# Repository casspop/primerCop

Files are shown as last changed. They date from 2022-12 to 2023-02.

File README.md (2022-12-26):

# PrimerCop

## A primer watchdog for a Hornady Lock-n-Load AP press

**The Problem:** If you forget to press the handle forward at the end of a loading cycle, 
the primer is not seated in the case.  

On a progressive press this is a problem.
It is a problem because the next step in the process is loading powder.  If there is not a primer plugging the primer cup when your 'finished' round is ejected into the tray, powder starts falling out the case generally making a mess.

That's why I designed PrimerCop.  It keeps track of how many primers I've used (secondary function), and it emits a long beep until I press the arm forward to seat the primer (primary function).

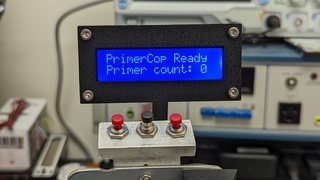
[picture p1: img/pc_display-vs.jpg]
PrimerCop display Introducing PrimerCop.

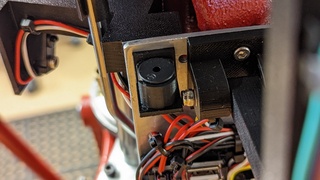
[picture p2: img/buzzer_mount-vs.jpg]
Closeup of the buzzer mount Closeup of the buzzer mount.

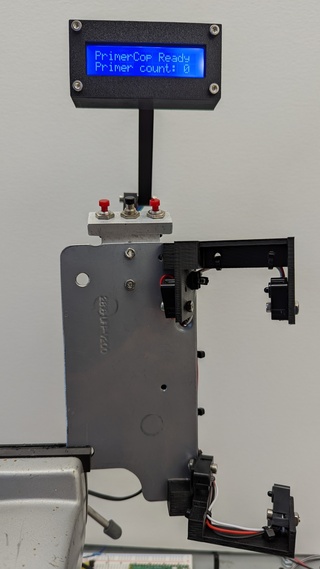
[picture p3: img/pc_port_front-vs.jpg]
portrait front Version 1.5 portrait.

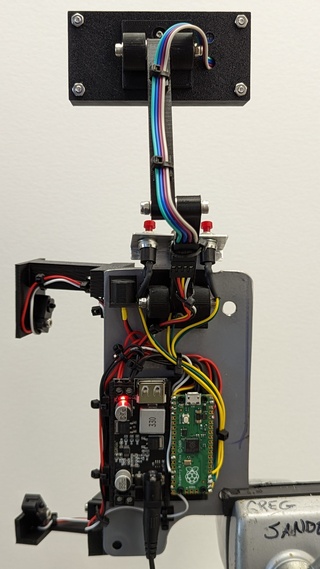
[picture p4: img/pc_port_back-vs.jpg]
portrait back Version 1.5 portrait.


All images are [here on the /img readme.md](./img/readme.md).

PrimerCop uses two sets of Adafruit IR break-beam sensors which are triggered at the top and bottom of the cycle.

A Drok buck converter provides power to a Raspberry Pi Pico microcontroller running a Micropython app I wrote.

The mounts for everything are designed in OpenSCAD and are currently printed in PLA on a Prusa Mk3s.  I had thought I might want to print the parts with ABS, but after trying it once, I decided to stick with PLA because it is stiffer, not to mention easier.

The whole thing is built on a steel plate that bolts to the press with two 1/4-20 bolts screwed into the factory provided holes on the back of the press.

This makes for easy removal of the entire unit for any reason at any time.

### Changelog
**12/23/22** - v1.1.0 of bottom bracket.  The primer slide wheel was contacting it ever so slightly, but it was enough to cause a problem. This mod takes care of that.</br>
             - v2.1.0 of main.py removes some unnecessary lines that were slowing things down.  Adding and subtracting to the count is quicker now.

**12/8/22** - Version 2 of the Pi Pico software is working and available in the Code
section.  Three hardware buttons were added. Two of them allow for adding or subtracting from the 'primercount' variable.  The third button resets everything.

Debouncing the buttons is done in software, and works pretty good.

**12/6/22** - Version 1 of PrimerCop is functioning.  It's not what I'd call ready
for prime time, but it does work.

I'm working on getting a set of 3 buttons added.  Designing the mounting
solution for the buttons is the task du jour.

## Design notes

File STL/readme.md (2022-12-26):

# STL Files

Here are the STL files I used on the Prusa Mk3s with PLA.

Be aware that the tolerances on these are tight.  You can construct the device using these STL's, but the hardware will go in only with some insistence on your part.  See the [readme.md in the docs folder](https://github.com/casspop/PrimerCop/blob/master/docs/Function%20and%20Assembly%20Notes.md) for more details.

Base for articulating arm (2 are needed). [ArticArm1602_base.stl](./ArticArm1602_base.stl)

Articulating arm section (2 needed). [ArticArm1602_sect.stl](./ArticArm1602_sect.stl)

Plastic version of my metal base plate. [horn_primercop_plate.stl](./horn_primercop_plate.stl)

Bottom of LCD mount. [hornady_1602_LCD_mount_bottom.stl](./hornady_1602_LCD_mount_bottom.stl)

Top of LCD mount. [hornady_1602_LCD_mount_top.stl](./hornady_1602_LCD_mount_top.stl)

Holder for electronics. [hornady_ap_primerCop_electronics-mnt.stl](./hornady_ap_primerCop_electronics-mnt.stl)

Top IR break-beam mount. [hornady_ap_primerCop_Top.stl](./hornady_ap_primerCop_Top.stl)

Bottom IR break-beam mount. [hornady_ap_primerCop.stl](./hornady_ap_primerCop.stl)

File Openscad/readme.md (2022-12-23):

# OpenSCAD files.

Built with [OpenSCAD](https://www.openscad.org).

These are the files I used to print the parts for PrimerCop.  

They are a bit tight on the hardware, but I was able to put it together.

I'm planning on adding about 1mm to the Drok power supply mount space as well
as the enclosure and faceplate for the LCD display.  I'll update these when
I do that, but it may be January or February 2023 before I get around to it.

- **1602A-4 LCD.scad** - the 16-character 2-line LCD module w/ i2c module attached.</br>
- **3mmSocketHeadHole.scad** - dependancy of several of these files.</br>
- **ArticArm1602_base.scad** - articulating arm base.</br>
- **ArticArm1602_sect.scad** - articulating arm section.</br>
- **horn_primercop_plate.scad** - renders the steel mounting plate. Corrected 12/10/22.</br>
- **hornady_1602_LCD_mount.scad** - The housing and faceplate for the 1602 LCD.</br>
- **hornady_ap_primerCop_electronics-mnt.scad** - mount for Drok and Pico.</br>
- **hornady_ap_primerCop_Top.scad** - top bracket for IR break-beams.</br>
- **hornady_ap_primerCop.scad** - bottom bracket for IR break-beams. v1.1.0 mod to avoid slide wheel.</br>
- **hw-061 i2c LCD module.scad** - i2c module. Goes with the LCD module.</br>
- **piezobuzzermount.scad** - mount for standard piezo buzzer.</br>
- **tinyZipTieMnt.scad** - glue these where you want to use a tiny zip tie.</br>

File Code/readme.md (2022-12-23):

# readme.md - What is What

**PrimerCop_Final_v2.1.1.py** - the Micropython software.  
v2.1.1 removed some unnecessary actions that slowed things down.
Rename this file to 'main.py' and upload it to the Pi Pico.

**lcd_api.py** - one of two driver files required.  Copy to the Pico.

**pico_i2c_lcd.py** - the second required file.  Copy to the Pico.

The two dependancy files are from here: [dhylands Github](https://github.com/dhylands/python_lcd)

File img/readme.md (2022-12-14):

# Images

Display
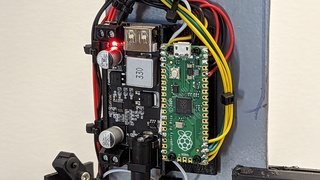
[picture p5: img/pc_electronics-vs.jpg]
Electronics

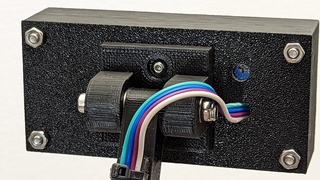
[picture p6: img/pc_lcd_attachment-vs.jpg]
LCD Attachment

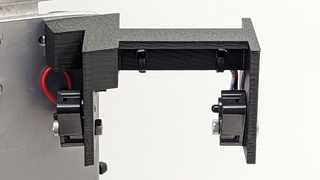
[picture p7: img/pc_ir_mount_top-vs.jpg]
Top Ir Mount

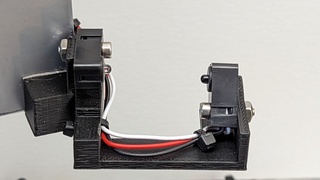
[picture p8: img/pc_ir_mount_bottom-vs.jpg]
Bottom Ir Mount

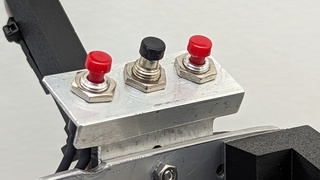
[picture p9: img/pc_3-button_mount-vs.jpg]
3-button mount.

Buzzer mount.
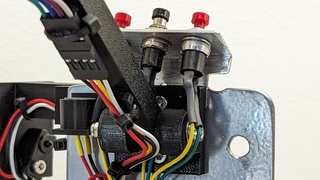
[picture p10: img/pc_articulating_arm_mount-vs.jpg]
Articulating arm mount.
</br>
Front View
Back View
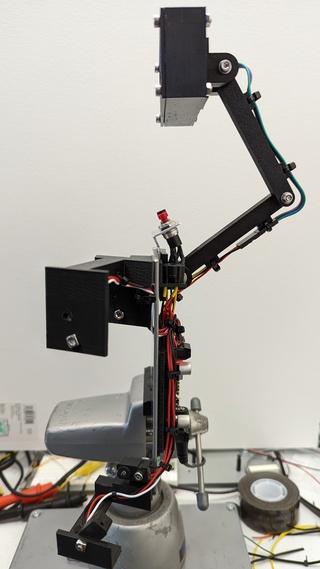
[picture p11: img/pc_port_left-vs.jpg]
Left Side View

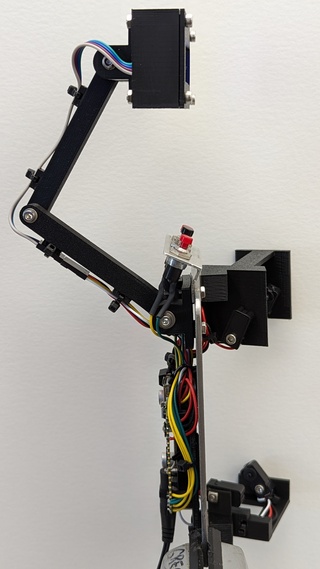
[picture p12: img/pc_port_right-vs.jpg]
Right Side View

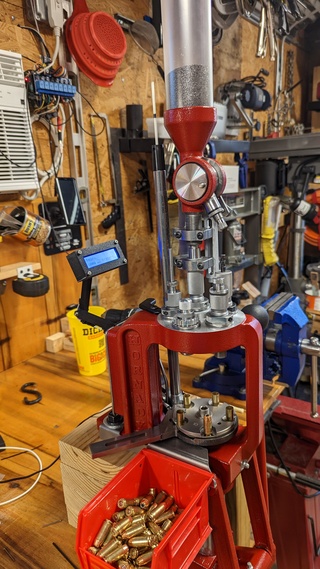
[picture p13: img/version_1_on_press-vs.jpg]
Version 1 hardware mounted on press.


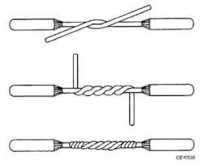
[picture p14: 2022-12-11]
img/lineman-splice.jpg

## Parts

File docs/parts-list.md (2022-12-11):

# Parts List

These are the parts I used to put this together.  Some of them, like fasteners and standoffs, are from kits I have on hand which were purchased for other projects.

The 3mm (1/8") plate I used as the primary mounting plate is a recycled VESA mount adapter plate from a flat panel display mounting kit I acquired years (decades!) ago.  As usual, I use what I have when I can.

All links below are for your convenience.  I get nothing from anyone for posting them. (CTRL-click links to open in new window.)

## The Parts

- [Raspberry Pi Pico](https://www.sparkfun.com/products/17829?src=raspberrypi) - $4.00 - the 'W' is not needed for this project.
- [Drok Buck Converter](https://www.amazon.com/gp/product/B01NALDSJ0/ref=ppx_yo_dt_b_search_asin_title?ie=UTF8&psc=1) - $9.99 - 12vdc to 5vdc power supply.  Plug a 12vdc wall wart in and you're ready to go.  You do have a bunch of those in a box somewhere, right?  I use this power supply a lot in my Pi projects.
- [Adafruit IR break-beam sensors](https://www.adafruit.com/product/2167) - $2.95 per set - Buy at least two sets, one for the top and one for the bottom.  I recommend having a spare in case you mess up.
- [SPST Momentary pushbuttons](https://www.amazon.com/dp/B0BHCLHNKR?psc=1&ref=ppx_yo2ov_dt_b_product_details) - $9.99 for 12 - Need three, but they're good to have on hand.  I like these with the pigtail already soldered on.  Convenient.
- [1602 LCD with i2c module](https://www.amazon.com/KEYESTUDIO-Display-Arduino-Raspberry-Stm32/dp/B0177XQE7K) - $9.99 - This is not the exact one I used, but they are very standardized, so it should be fine.
- [M3 Hex Socket Head screws](https://www.amazon.com/gp/product/B07J44YXV3/ref=ppx_yo_dt_b_search_asin_title?ie=UTF8&psc=1) - $21.99 for 700 piece kit - You really need to have these on hand.
- [M2.5 Stainless Steel Button Head Socket Cap Screws](https://www.amazon.com/gp/product/B076ZN18KZ/ref=ppx_yo_dt_b_search_asin_title?ie=UTF8&psc=1) - $11.99 for 240 pieces - Great kit.
- [M2.5 Nylon Standoffs](https://www.amazon.com/gp/product/B07D78PFQL/ref=ppx_yo_dt_b_search_asin_title?ie=UTF8&psc=1) - $14.88 for 320 piece kit - Again, invaluable if you're doing much project work like this.
- [4" Zip Ties](https://www.amazon.com/s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) - $5-7 - Nothing special here.  Home Depot, Lowes, Ace Hardware.
- [Gorilla Mounting Tape](https://www.amazon.com/Gorilla-Heavy-Double-Sided-Mounting/dp/B082TQ3KB5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) - $12.24 for 120 inches - This stuff is fantastic if you want a thing to stay where you put it.  Available nearly anywhere.
- [Stainless washers](https://www.amazon.com/gp/product/B009OK7GPO/ref=ppx_yo_dt_b_search_asin_title?ie=UTF8&psc=1) - $6.16 for 100 - Needed for articulating arm joints.  You can use other things, but these are what I have.
- [M3 Stainless NyLock Nuts](https://www.amazon.com/100Pcs-Stainless-Self-Lock-Inserted-Clinching/dp/B075ZZW7VL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) - $6.99 for 100 - Use on articulating arm pivot points.
- [3/4" Aluminum angle stock 1/8" thick](https://www.homedepot.com/p/Everbilt-3-4-in-x-36-in-Aluminum-Angle-with-1-8-in-Thick-801397/204273997) - $11.47 for 36" - Need about 2" of this, but again, it's good to have on hand.  Used for the switch mount.
- Heat Shrink Tubing of appropriate sizes.  Get an assortment set if you don't have some already.

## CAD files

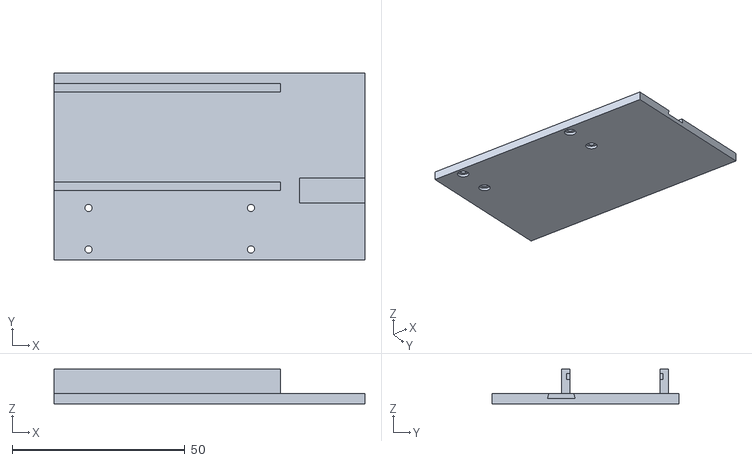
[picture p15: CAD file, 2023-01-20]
STL/hornady_ap_primerCop_electronics-mnt.stl
90.0 x 54.0 x 10.0

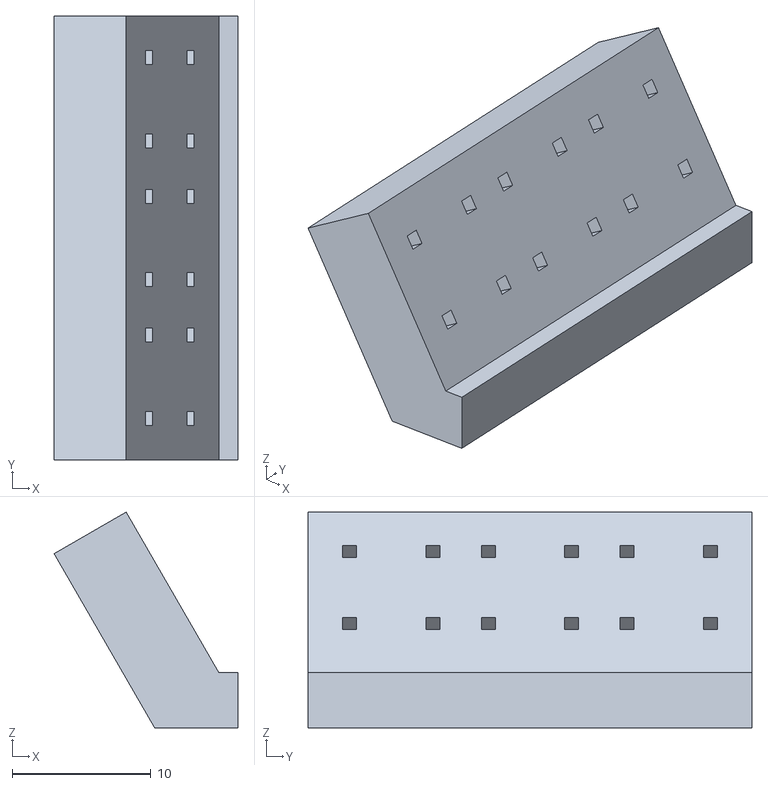
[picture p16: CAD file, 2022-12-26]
STL/horn_PrimerCop_buttons_base.stl
13.2 x 32.0 x 15.6

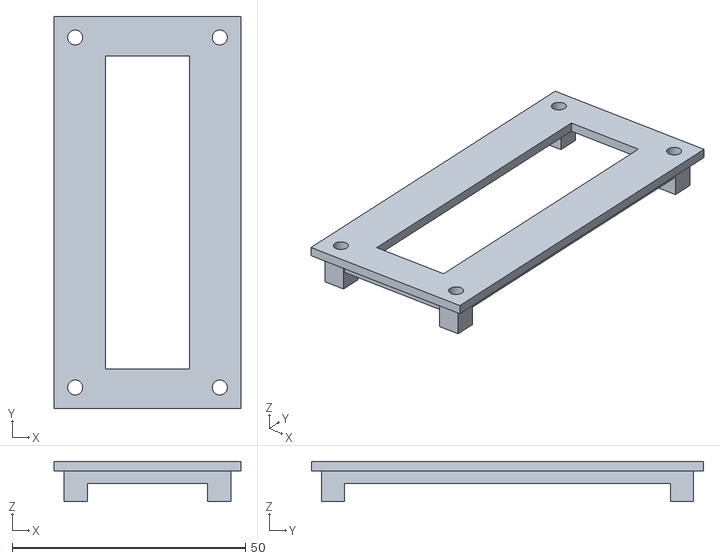
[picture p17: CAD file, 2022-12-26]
STL/hornady_1602_LCD_mount_top.stl
40.0 x 84.0 x 8.60

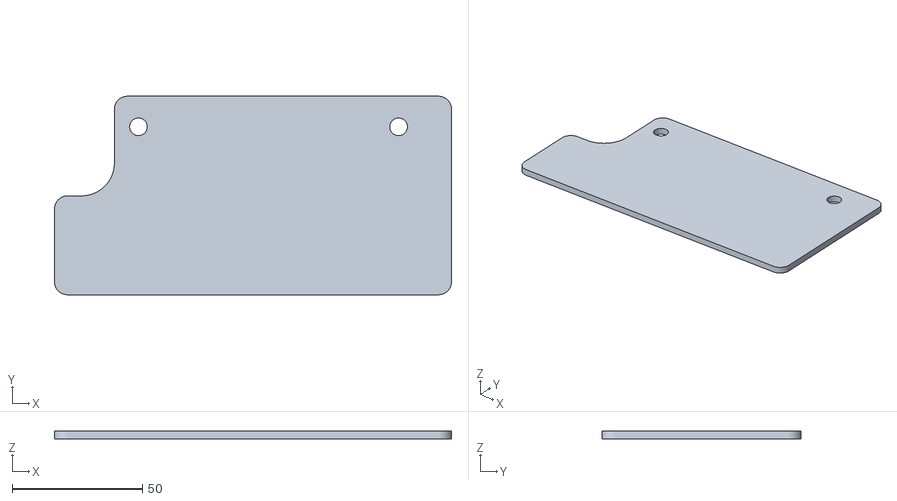
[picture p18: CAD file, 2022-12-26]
STL/horn_primercop_plate.stl
152.5 x 76.3 x 3.00

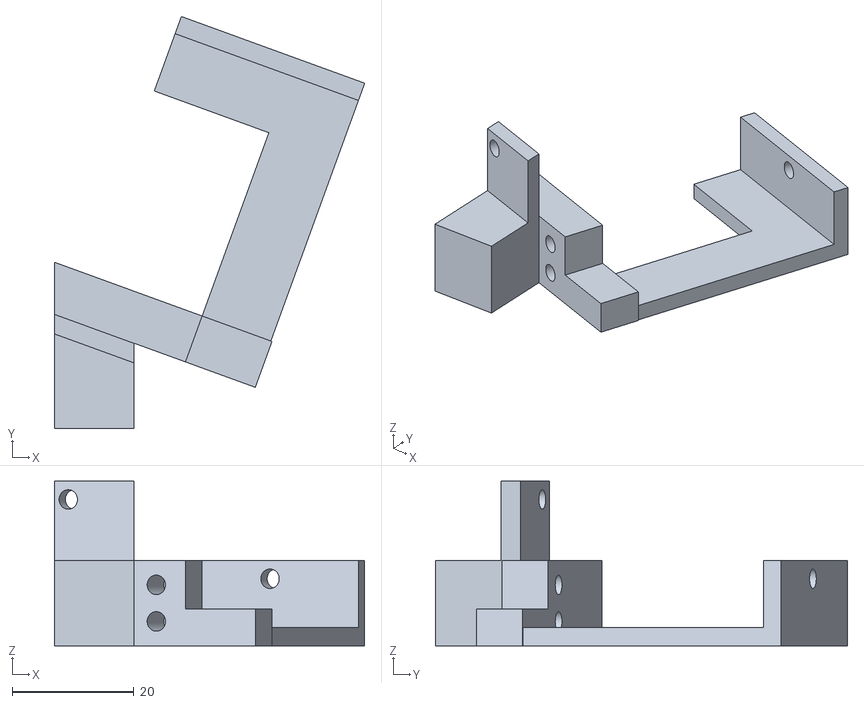
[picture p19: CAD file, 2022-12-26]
STL/hornady_ap_primerCop.stl
50.9 x 67.6 x 27.0

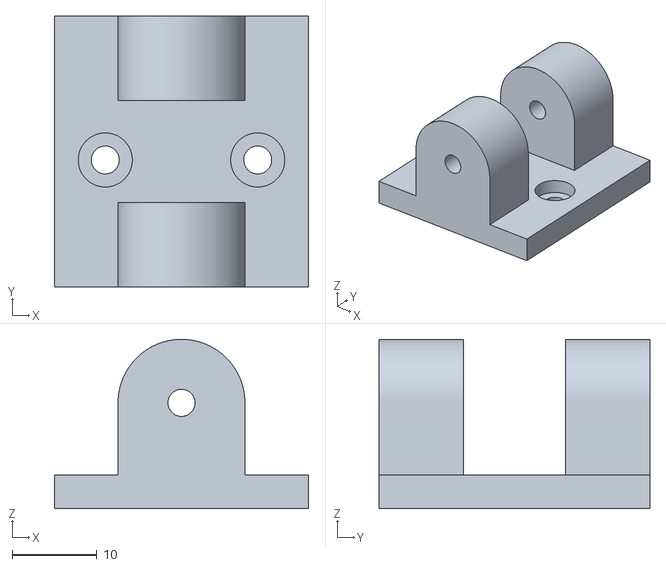
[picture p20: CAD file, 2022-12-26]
STL/ArticArm1602_base.stl
30.0 x 32.0 x 20.0

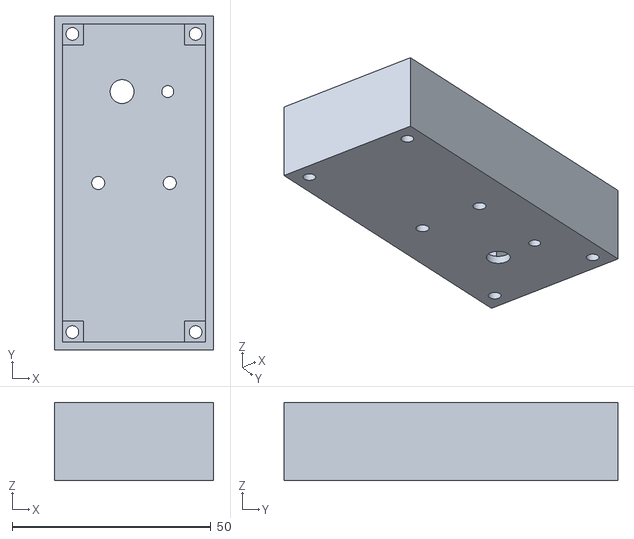
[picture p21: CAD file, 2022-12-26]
STL/hornady_1602_LCD_mount_bottom.stl
40.0 x 84.0 x 19.7

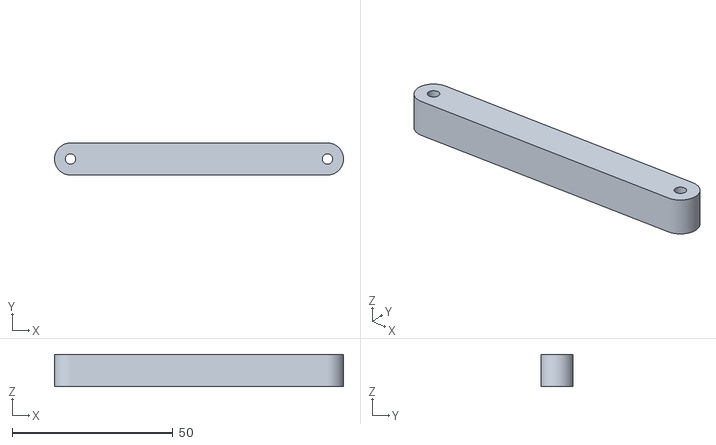
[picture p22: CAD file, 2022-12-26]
STL/ArticArm1602_sect.stl
90.0 x 10.0 x 10.0

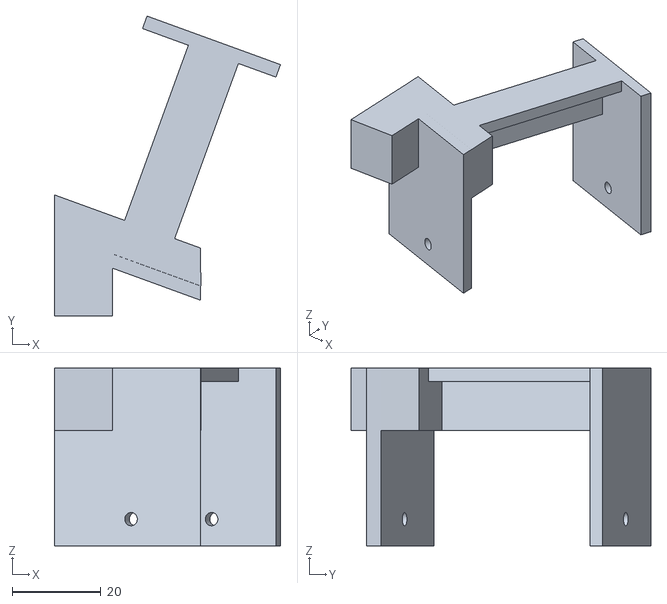
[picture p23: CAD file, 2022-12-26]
STL/hornady_ap_primerCop_Top.stl
50.9 x 67.6 x 40.0

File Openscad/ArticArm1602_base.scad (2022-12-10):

// ArticArm1602_base.scad - Articulating Arm Mount for 1602A LCD
// 2022 Gregory A Sanders
//
//
// hole for 3mm machine screw = 3.2
//

use <3mmSocketHeadHole.scad>

$fn=120;
module base(){
    difference(){
        cube([30,32,4]);
        rotate([180,0,0])
        translate([6,-15,-6])
        SocHdHole();      
        rotate([180,0,0])
        translate([24,-15,-6])
        SocHdHole();

    }
}

module pivot(){
    difference(){
        translate([0,0,12.5])
        rotate([90,0,0])
        hull(){
            cylinder(10,d=15,center=true);
            translate([0,-7.5,0])
            cube([15,10,10],true);
        }
        union(){
        translate([0,0,12.5])
        rotate([90,0,0])
        cylinder(30,d=3.2,center=true);

        }
    }
}

module aacomposite(){
    base();
    translate([15,5,0])
    pivot();
    translate([15,27,0])
    pivot();
}

aacomposite();

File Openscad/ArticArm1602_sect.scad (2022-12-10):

//ArticArm1602_sect.scad - Articulating Arm section for 1602 LCD
//2022 Gregory A Sanders
//
//
$fn=120;
module arm(){
    difference(){
    hull(){
        translate([0,5,0,])
        cylinder(10,d=10);
        cube([80,10,10]);
        translate([80,5,0])
        cylinder(10,d=10);
    }
    translate([0,5,-5])
    cylinder(20,d=3.2);
    translate([80,5,-5])
    cylinder(20,d=3.2);
}
}
arm();

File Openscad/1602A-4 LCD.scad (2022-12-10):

//1602A-4 LCD.scad - Dr.Gerg's 1602A-4 16x2 LCD module
//
// OpenSCAD definition file
// https://www.drgerg.com

use <hw-061 i2c LCD module.scad>;
holespcx = 33.86;
holespcy = 77.9;
mntholedia = 2.7;
pcb1 = [36,80,1.13];
lcd = [24.40,69.28,6.57];
lscrn = [16.28,65.19,1]; // lcd screen
lsc = [1,0.1,0];                    // lcd screen corner
LEDpoly = [[2.625,0],[15.125,0],[17.75,3.25],[17.75,5.35],[0,5.35],[0,3.25]];
module pin(tx,ty,tz,ry,cl,cx,cy){
    translate([tx,ty,tz])
    rotate([0,ry,0])
    cube([cl,cx,cy],false);
    translate([-2,-1,5])
    color("black")
    cube([40.5,2.54,2.54],false);
}
module screen(){
    minkowski(){
        cube([lscrn.x - lsc.x*2,lscrn.y - lsc.x*2,lscrn.z]);
        cylinder(r=lsc[0],h=lsc[1]);
    }
}
module light(){
    linear_extrude(3)
    polygon(LEDpoly);
    }
$fn=48;

module LCD1602A(){
    difference(){
    color("green")
    cube(pcb1);
    translate([(pcb1.x/2)-((holespcx-mntholedia)/2),(pcb1.y/2)-((holespcy-mntholedia)/2),0])
    cylinder(h=6,d=mntholedia,center=true);
    translate([(pcb1.x/2)+((holespcx-mntholedia)/2),(pcb1.y/2)-((holespcy-mntholedia)/2),0])
    cylinder(h=6,d=mntholedia,center=true);
    translate([(pcb1.x/2)-((holespcx-mntholedia)/2),(pcb1.y/2)+((holespcy-mntholedia)/2),0])
    cylinder(h=6,d=mntholedia,center=true);
    translate([(pcb1.x/2)+((holespcx-mntholedia)/2),(pcb1.y/2)+((holespcy-mntholedia)/2),0])
    cylinder(h=6,d=mntholedia,center=true);
    };
    translate([pcb1.x/2 - 17.25/2,0,pcb1.z])
    color("white")
    light();
    difference(){
        color("black")
        translate([pcb1.x/2 - lcd.x/2,pcb1.y/2 - lcd.y/2,pcb1.z])
        cube(lcd);
        color("blue")
        translate([pcb1.x/2 - lscrn.x/2 +lsc.x,pcb1.y/2 - lscrn.y/2 + lsc.x,lcd.z-lscrn.z+1.1])
        screen();
    }
    translate([33.3,33.9875,-7.7])
    rotate([0,0,90])
    for (i=[0:15])
        pin(i*2.54,0,0,270,12,.64,.64);
    translate([34.3,32.4,-3])
    rotate([0,180,0])
    hw061();
}

LCD1602A();

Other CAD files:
Openscad/3mmSocketHeadHole.scad
Openscad/horn_primercop_plate.scad
Openscad/hornady_1602_LCD_mount.scad
Openscad/hornady_ap_primerCop.scad
Openscad/hornady_ap_primerCop_Top.scad
Openscad/hornady_ap_primerCop_electronics-mnt.scad
Openscad/hw-061 i2c LCD module.scad
Openscad/piezobuzzermount.scad
Openscad/tinyZipTieMnt.scad

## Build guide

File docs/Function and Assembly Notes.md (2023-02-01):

# Function and Assembly Notes

**--== These notes are in progress ==--**

## Function Notes

PrimerCop is a pretty simple piece of gear.  The bar on the press that retrieves and delivers the primers moves up and down with the turret plate.  We are putting IR break-beam sensors at the top and bottom of its travel to detect its location in the cycle.

The sensor at the top is triggered by the bar blocking the IR light.  When that happens, the program provides feedback to the user and increments the counter.

As the bar moves back down, the sensor is once again exposed to the IR emitter's output, and the software provides notification of that event.

When the bar reaches the bottom of its travel, the bottom sensor is deprived of IR and the software interprets that event as a primer is ready to be seated.  The buzzer begins sounding and continues until the handle of the press is moved forward to seat the primer in the case.

Moving the handle forward lowers the turret and the bar.  This exposes the sensor to the IR source and the software stops the buzzer and informs the user that the primer has been seated.

Releasing the handle once again blocks the sensor, and the software then reports the end of the cycle and how many primers have been used to that point.

## Assembly Notes: refer to the pictures in the ./img folder for reference

### Mounting sensor brackets

The top and bottom sensor brackets are held to the mount plate with Gorilla double-sided mounting tape.  This solution seems to be more than adequate.  Of course, screws and nuts could be used, but I don't see why that would be necessary at this point.

### IR sensor notes

The sensors themselves are not mounted exactly the same on top and bottom.  That is because the little primer sled moves out into the area where the top emitter would be if it were mounted exactly like the bottom emitter.  What I did was to dry-fit the emitter with the assembled PrimerCop mounted to the press.  I determined where a hole needed to be drilled in the top bracket so the emitter's LED could cast its beam toward the receiver.  Then I drilled said hole and mounted the emitter.

### Base plate thoughts

I made my baseplate out of a steel VESA adapter plate from a TV mount.  I've had a few of these for years, and it was perfect for this application.  I cut out what I needed.

After getting the PrimerCop working, I then made the OpenSCAD model to match the dimensions of my steel plate.  I printed it out and verified its fit on the press.  I'm of the opinion at this point that a 3D printed version of that plate in PLA or PETG with no infill (solid plastic) would be adequately stiff to be used in place of the steel plate I have.  Just a thought.

### Mounting electronics

The Drok power supply and the Pi Pico are mounted to the same plate.  The Drok converter has no holes for mount screws, so I have a channel for it to slide into.  It is a bit too tight, but I was able to work it into position.  I made a version 2 of the hardware with about 1.0mm added to make it less tight. That's what is in the SCAD and STL folders now.

There are holes in the mount plate for 2.5mm standoff screws.  Attach standoffs using those screws and mount the Pico to the standoffs.

Once you have both pieces of hardware mounted to their mount plate, affix it to the steel plate with 3 or 4 smallish pieces of Gorilla mounting tape.

### Display notes

The same snugness problem that I encountered with the Drok converter reared its ugly head with the display mount.  I will be adding some space to the interior of that model as well.  It =does= fit, but it's really tight.  Not so tight as to cause alarm, but too tight for easy assembly.

I also will be enlarging and moving the LCD contrast adjustment hole to more correctly align it with the potentiometer on the i2c board.  For the time being, I simply drilled it out larger so I could access the pot.

### Wire routing

As you assemble your parts, you will need to account for routing and dressing your wires.  I created the 'tinyZipTieMnt' model and I used it in several places where I needed them to keep wires under control.

I used a typical superglue (Cyanoacrylate) product.  I noticed it seemed to take an unusual amount of time for this glue to set on the plastic.  If I could be patient or distract myself with something long enough, it would eventually set.  Once it did, it was quite permanent.

You may need to drill some holes for zip ties in some areas.  Use your own judgement.

### Wiring diagram notes

There currently is no wiring diagram.  I may fix that later, but it's not a high priority.

- The i2c circuit is typical.
- I landed 12vdc from the Drok on the VSYS pad.  I had it on the VBUS pad originally, but moved it while trying to comprehend the parameters of using USB for programming without unplugging the Drok supply.  In the end, I just left my 12vdc supply connected to VSYS.  VBUS may be a better choice, but it also has a voltage drop from a diode.  No biggie, but it is there.
- Where to land the sensors and switches can be determined by reading the Python program file.  easy peasey
- Be very careful to provide solid power and ground connections between the Drok converter and the Pico.
  - If you, like I, use the phoenix connector on the Drok, make sure you get all your conductors solidly screwed down.  
  - This does NOT mean tighten the screw more.  It means strip off enough insulation to expose enough conductor so when you twist them all together they are long enough to fit deep into the connector, but not so long as to have bare conductor sticking out more than 1/32" or so.  If you need to, pull them back out and trim them off a bit.
- I create a splice point inline when I have a bunch of wires all going to the same place.  Just twist them together using a modified [linemans splice](../img/lineman-splice.jpg) (simplified) with one wire exiting to solder to the termination point.  The appropriate piece of heat shrink tube tops it off nicely.

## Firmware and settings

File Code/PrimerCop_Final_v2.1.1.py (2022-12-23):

# PrimerCop_Final.py for Micropython on Pi Pico
# Copyright (C) 2022 Gregory A Sanders
# Rename to main.py and upload to Pico
# along with lcd_api.py and pico_i2c_lcd.py
# v2.1 - December 2022
#
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
from utime import sleep, sleep_ms
import utime
from machine import Pin, PWM, I2C, Timer
import micropython
from pico_i2c_lcd import I2cLcd

i2c = I2C(0, sda=Pin(0), scl=Pin(1), freq=400000)
I2C_ADDR = i2c.scan()[0]
lcd = I2cLcd(i2c, I2C_ADDR, 2, 16)

micropython.alloc_emergency_exception_buf(100)
buzzer = PWM(Pin(2))
topIR = Pin(12, Pin.IN, Pin.PULL_UP)
bottomIR = Pin(14, Pin.IN, Pin.PULL_UP)
pausepin = Pin(16, Pin.IN, Pin.PULL_UP)
pluspin = Pin(17, Pin.IN, Pin.PULL_UP)
minuspin = Pin(18, Pin.IN, Pin.PULL_UP)

timer = Timer()

status = {12:0,14:3,16:0,17:0,18:0}
primercount = 0



def db16(pin):
    timer.init(mode=Timer.ONE_SHOT, period=400, callback=cb16)

def db17(pin):
    timer.init(mode=Timer.ONE_SHOT, period=400, callback=cb17)

def db18(pin):
    timer.init(mode=Timer.ONE_SHOT, period=400, callback=cb18)

def buzz():
    buzzer.freq(500)
    buzzer.duty_u16(1000)
    sleep(0.1)
    buzzer.duty_u16(0)

def beep():
    buzzer.freq(800)
    buzzer.duty_u16(1000)
    sleep(0.1)
    buzzer.duty_u16(0)

def warn():
    buzzer.freq(500)
    buzzer.duty_u16(1000)


def irqsetup():
    topIR.irq(trigger=Pin.IRQ_FALLING | Pin.IRQ_RISING, handler=cb12)
    bottomIR.irq(trigger=Pin.IRQ_FALLING | Pin.IRQ_RISING, handler=cb14)

    pluspin.irq(trigger=Pin.IRQ_FALLING, handler=db16)
    minuspin.irq(trigger=Pin.IRQ_FALLING, handler=db17)
    pausepin.irq(trigger=Pin.IRQ_FALLING, handler=db18)

def cb12(pin):
    global status,primercount
  
    if pin.value()==0:                 # blocked
        primercount = primercount + 1
        lcd.clear()
        lcd.putstr("Get primer " + str(primercount))
        status[12] = 1
        status[14] = 0
        buzz()

    if pin.value()==1:                # cleared
        status[12] = 0
        lcd.clear()
        lcd.putstr("Loaded primer " + str(primercount))
        beep()

def cb14(pin):
    global status,primercount
    if status[14] == 0 and pin.value() == 0:      ## blocked going down
        status[14] = 1
        lcd.clear()
        lcd.putstr("Seat primer.")
        warn()

    if status[14] == 1 and pin.value() == 1:      ## cleared going down
        status[14] = 2
        lcd.clear()
        lcd.putstr("Seating.")
        beep()
        sleep(0.2)

    if status[14] == 2 and pin.value() == 0:      ## blocked going up
        lcd.clear()
        lcd.putstr("Ready")
        lcd.move_to(0,1)
        if primercount == 1:
            primer = "primer"
        else:
            primer = "primers"
        lcd.putstr("Used " + str(primercount) + " " + primer + ".")
        status[14] = 3

def cb16(tim):
    global status,primercount
    status[16] += 1
    primercount += 1
    lcd.clear()
    lcd.putstr("Add 1 primer.")
    lcd.move_to(0,1)
    lcd.putstr("Count is : " + str(primercount))
    # sleep(1)
    # lcd.clear()
    # lcd.putstr("Ready")
    # lcd.move_to(0,1)
    # lcd.putstr("Primer count: " + str(primercount))

def cb17(tim):
    global status,primercount
    status[17] += 1
    primercount -= 1
    lcd.clear()
    lcd.putstr("Minus 1 primer.")
    lcd.move_to(0,1)
    lcd.putstr("Count is : " + str(primercount))
    # sleep(1)
    # lcd.clear()
    # lcd.putstr("Ready")
    # lcd.move_to(0,1)
    # lcd.putstr("Primer count: " + str(primercount))


def cb18(tim):
    global status,primercount
    status = {12:0,14:3,16:0,17:0,18:0}
    primercount = 0
    lcd.clear()
    lcd.putstr("Reset")
    sleep(2)
    lcd.clear()
    lcd.putstr("PrimerCop Ready")
    lcd.move_to(0,1)
    lcd.putstr("Primer count: " + str(primercount))

irqsetup()
lcd.clear()
lcd.putstr("PrimerCop v2.1")
lcd.move_to(0,1)
lcd.putstr("2022 drgerg.com")
sleep(3)
lcd.clear()
lcd.putstr("PrimerCop Ready")
lcd.move_to(0,1)
lcd.putstr("Primer count: " + str(primercount))

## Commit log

2022-12-08 remove button-base.scad
    [horn_PrimerCop_buttons_base.scad]
2022-12-10 add .scad for steel plate
    [horn_primercop_plate.scad]
2022-12-10 add ziptie mount .scad
    [tinyZipTieMnt.scad]
2022-12-10 add buzzer mount
    [piezobuzzermount.scad]
2022-12-10 Correct hole placement.
    [horn_primercop_plate.scad]
2022-12-10 correct thickness
    [horn_primercop_plate.scad]
2022-12-10 correct mount holes
    [horn_primercop_plate.scad]
2022-12-10 adjust mount holes
    [horn_primercop_plate.scad]
2022-12-11 add i2c module .scad
    [hornady_1602_LCD_mount.scad, hw-061 i2c LCD module.scad]
2022-12-11 small update
    [hornady_1602_LCD_mount.scad]
2022-12-11 add missing dependancies
    [3mmSocketHeadHole.scad, hornady_1602_LCD_mount.scad]
2022-12-11 LCD mount update
    [hornady_1602_LCD_mount.scad]
2022-12-11 clean up LCD_mount a bit.
    [hornady_1602_LCD_mount.scad]
2022-12-19 Update Function and Assembly Notes.md
2022-12-23 v1.1.0 mod
    [hornady_ap_primerCop.scad]
2022-12-23 v1.1.0 mod update
    [hornady_ap_primerCop.scad]
2022-12-26 STL uploads
    [ArticArm1602_base.stl, ArticArm1602_sect.stl, horn_PrimerCop_buttons_base.stl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]
2023-01-20 widen DROK slot
    [hornady_ap_primerCop_electronics-mnt.scad]

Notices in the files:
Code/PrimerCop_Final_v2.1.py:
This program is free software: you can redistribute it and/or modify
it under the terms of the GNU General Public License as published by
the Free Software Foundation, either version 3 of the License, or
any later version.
